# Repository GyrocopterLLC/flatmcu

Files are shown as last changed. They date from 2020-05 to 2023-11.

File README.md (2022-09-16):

# flatmcu
Hardware design for the flatmcu - an STM32G4 based BLDC / FOC motor controller.

## Features
All schematic and layout was created with KiCad EDA (https://kicad.org).

The controller is based on the STM32G473CB microcontroller from ST Microelectronics. It contains an ARM Cortex-M4 core at up to 170MHz. The three-phase bridge driver is the TI DRV8353RS, which also contains shunt resistor current sensors and a 95V buck regulator.

The MOSFETs in the three-phase bridge (Toshiba TPW4R50ANH) are dual-side cooling. There's a large metal pad on top of them. A heatsink should be attached there. The opposite side of the board is intended for soldering on the large battery and phase wires.

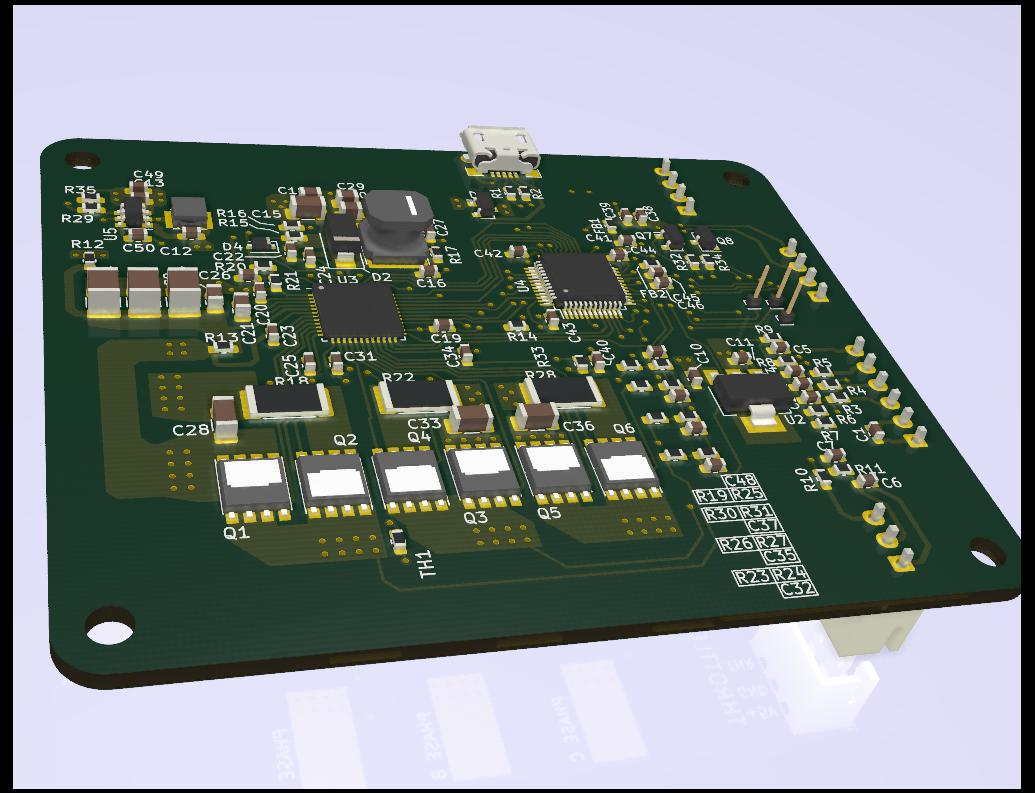
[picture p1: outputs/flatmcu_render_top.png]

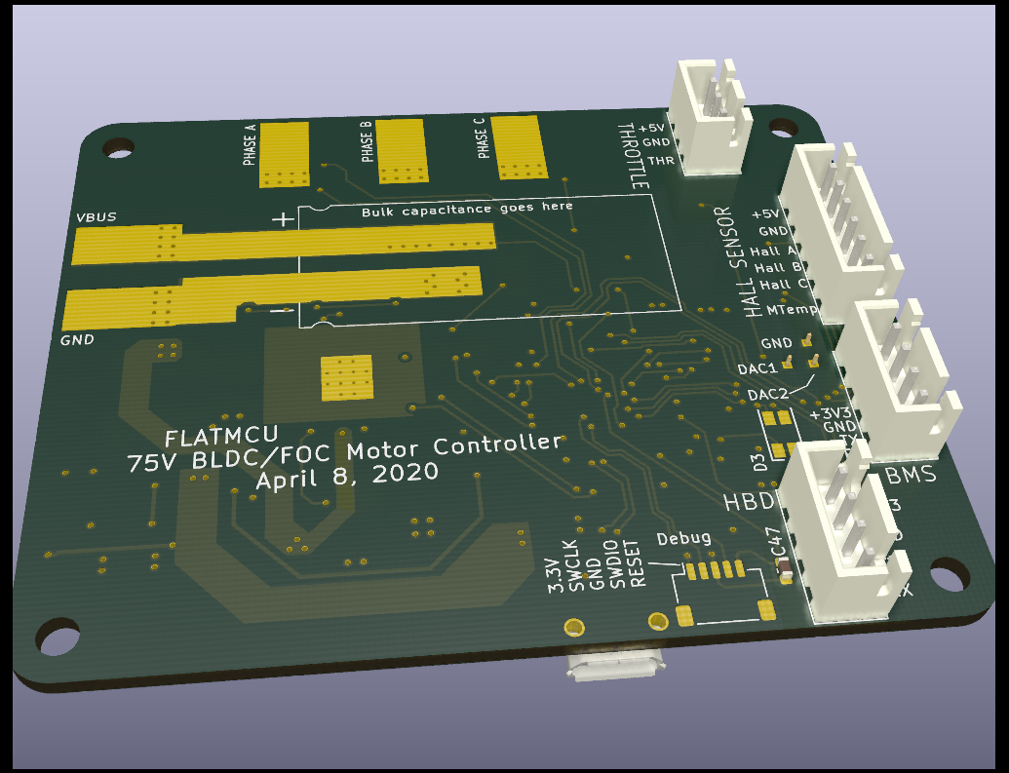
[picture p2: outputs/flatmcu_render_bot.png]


## Schematic
### Main
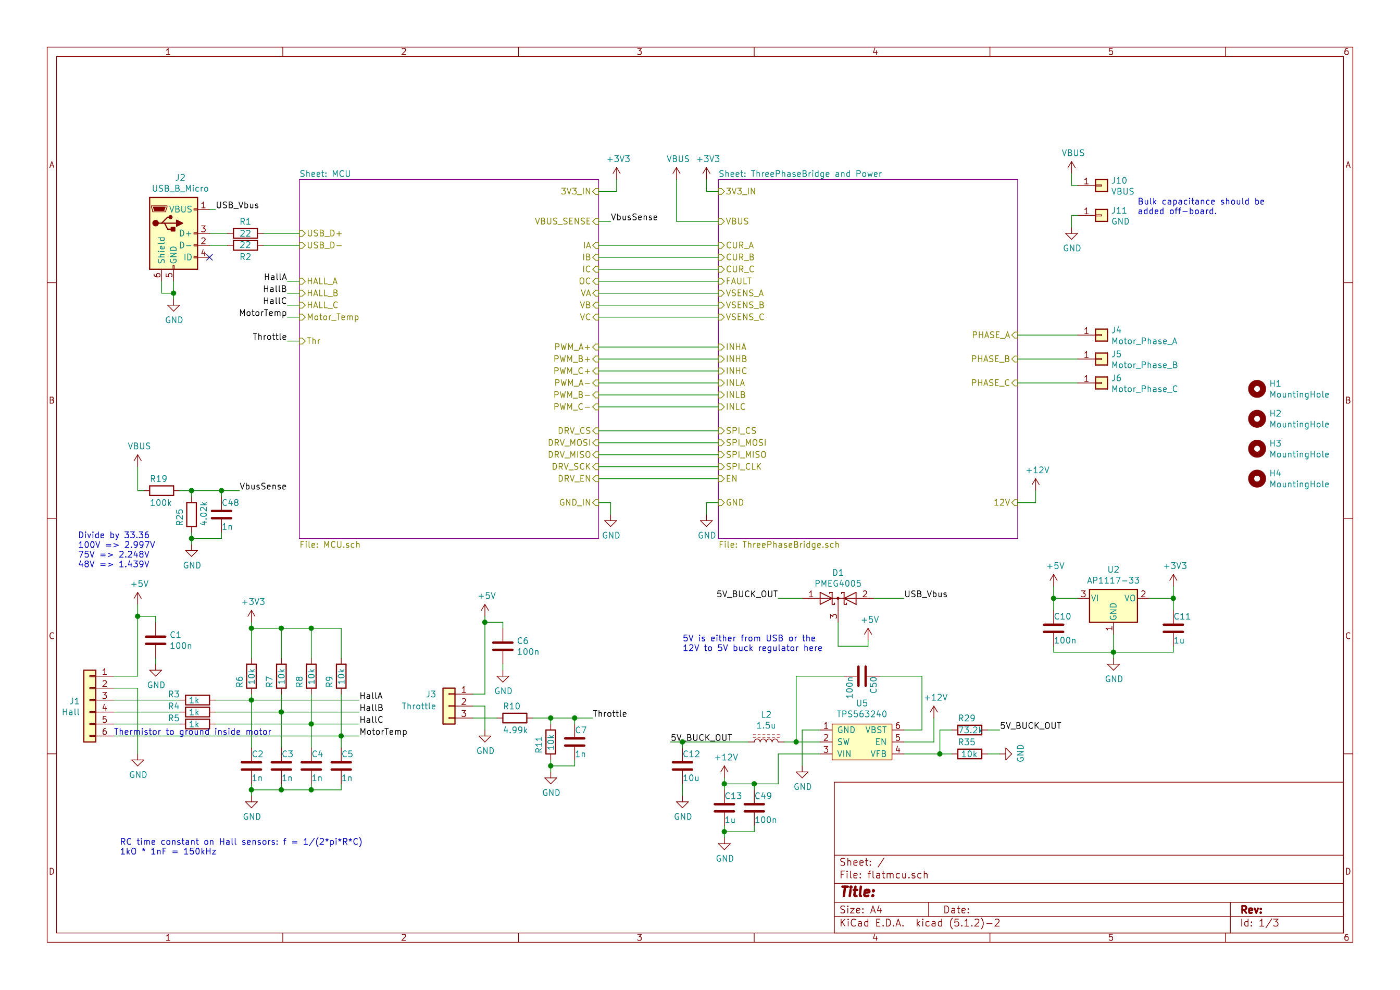
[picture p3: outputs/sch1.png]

### Microcontroller
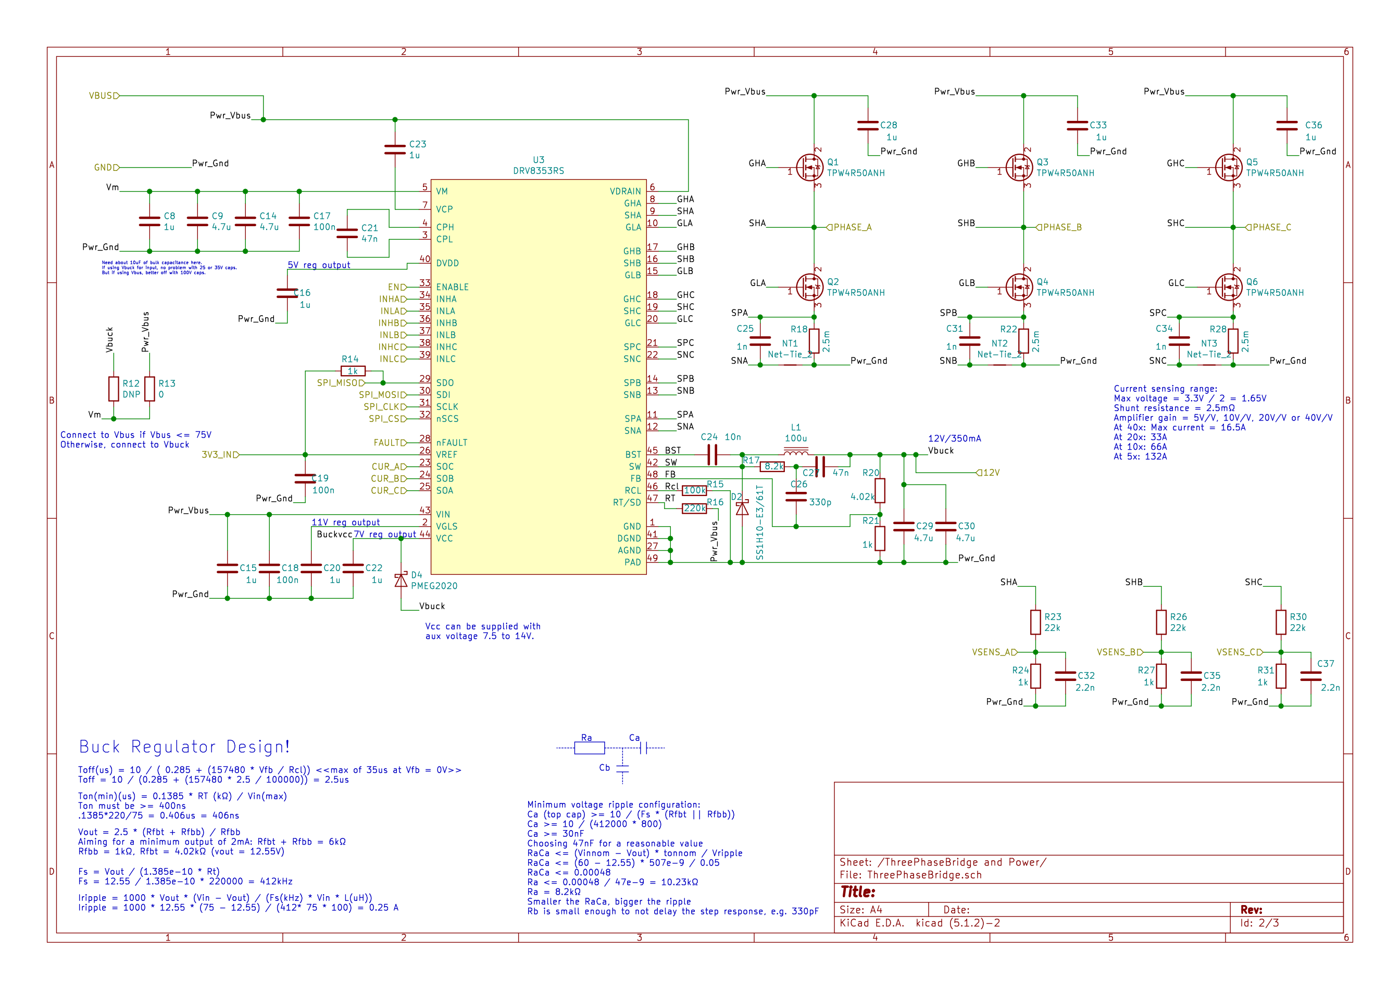
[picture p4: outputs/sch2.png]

### Three-phase bridge
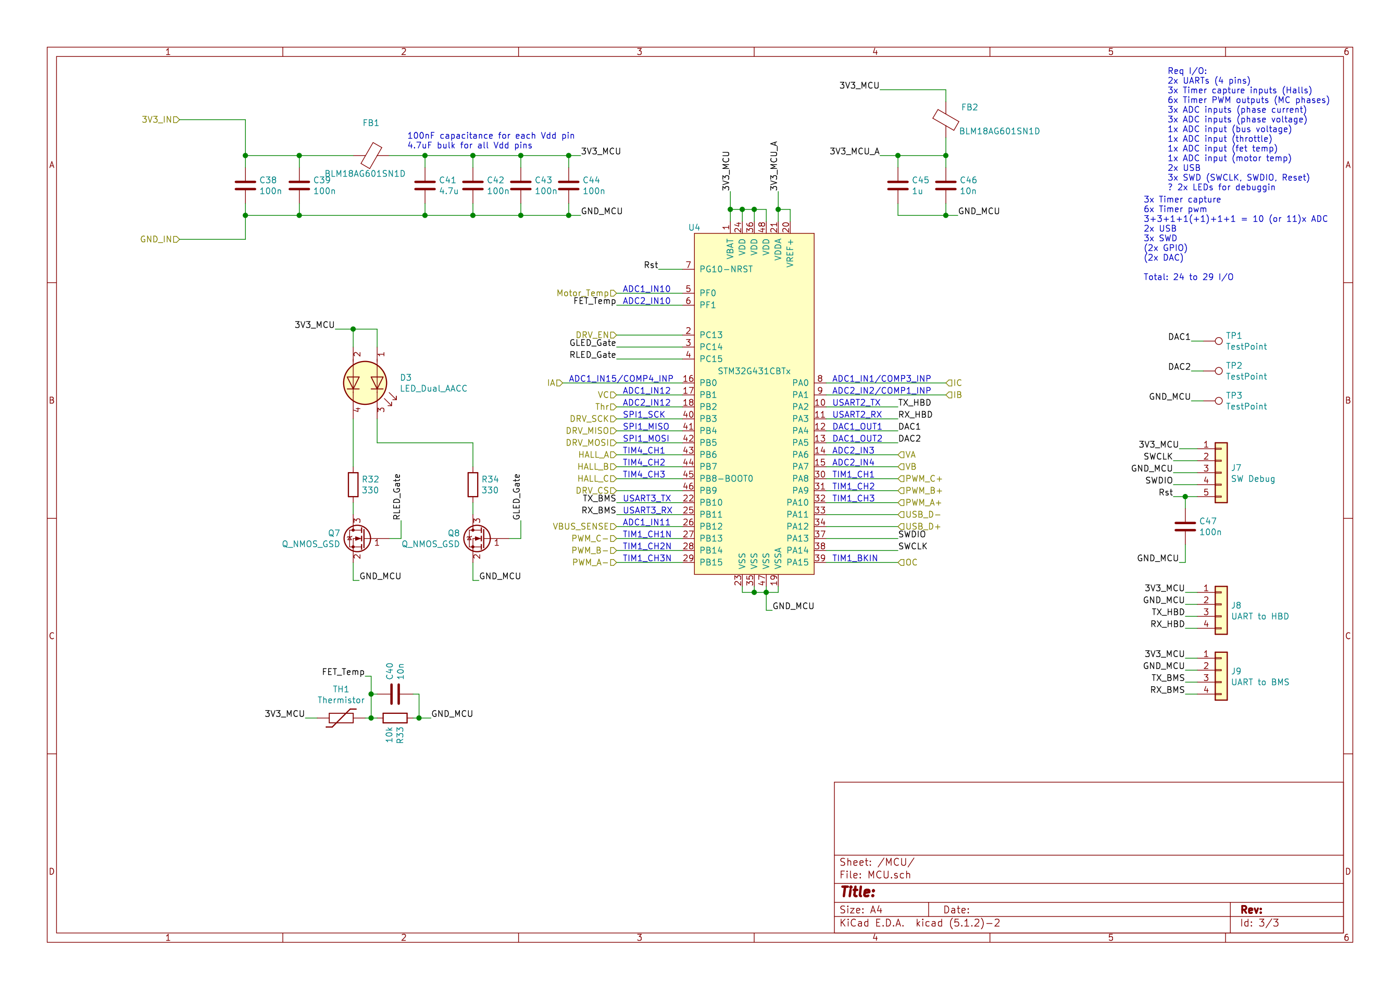
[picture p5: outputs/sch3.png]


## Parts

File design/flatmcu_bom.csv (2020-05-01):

*** Bill of Materials ***
* Note: Many of the resistors and capacitors do not have specific part numbers listed. Substitute with any that meet the value / footprint / voltage specs. *
* Suggest to use X5R/X7R capacitors or better. *
Part No | Value | Footprint | Qty | Refs
??? | 100n/100V | C0805 | 2 | C17, C18
CL10A104KA8NNNC | 100n/25V | C0603 | 11 | C1,C10,C19,C38, C42, C43, C44, C47, C49, C50, C6
??? | 1u/16V | C0603 | 8 | C11, C13, C16, C20, C22, C23, C39, C45
??? | 10n/50V | C0603 | 3 | C24, C40, C46
CRM188R61A106KE69D | 10u/10V | C0603 | 1 | C12
??? | 1n/50V | C0603 | 9 | C2, C3, C4, C5, C7, C25, C31, C34, C48
GCM21BC72A105KE36L | 1u/100V | C0805 | 5 | C8, C15, C28, C33, C36
??? | 2.2n/50V | C0603 | 3 | C32, C35, C37
??? | 330p/50V | C0603 | 1 | C26
??? | 4.7u/6.3V | C0603 | 1 | C41
??? | 4.7u/16V | C0805 | 2 | C29, C30
GCM32DC72A475KE02L | 4.7u/100V | C1210 | 2 | C9, C14
??? | 47n/16V | C0603 | 1 | C27
CL21B473KCCWPNC | 47n/100V | C0805 | 1 | C21
PMEG4005CT,215 | Dual Schottky 40V 500mA | SOT23 | 1 | D1
SS1H10-E3/61T | Schottky 100V 1A | SMA | 1 | D2
LTST-C155GEKT | Red/Green LED | 4-SMD | 1 | D3
PMEG2020EJ,115 | Schottky 20V 2A | SOD323F | 1 | D4
TPW4R50ANH | N-CH 100V 92A | 8DSOP | 6 | Q1, Q2, Q3, Q4, Q5, Q6
AO3400A | N-CH 30V 6.7A | SOT23 | 2 | Q7, Q8
NR6045T101M | 100uH 800mA | 6x6mm | 1 | L1
SRN3015-1R5Y | 1.5uH 2.1A | 3x3mm | 1 | L2
BLM18AG601SN1D | Ferrite Bead 600ohm | R0603 | 2 | FB1, FB2
??? | 0R | R0603 | 1 | R13
??? | 33R | R0603 | 2 | R1, R2
??? | 330R | R0603 | 2 | R32, R34
??? | 100k | R0603 | 2 | R15, R19
??? | 10k | R0603 | 7 | R6, R7, R8, R9, R11, R33, R35
??? | 1k | R0603 | 8 | R3, R4, R5, R14, R21, R24, R27, R31
ERJ-M1WTF2M0U | 0R002 | R2512 | 3 | R18, R22, R28
ERJ-3EKF2203V | 220k | R0603 | 1 | R16
??? | 22k | R0603 | 3 | R23, R26, R30
??? | 4.02k | R0603 | 2 | R20, R25
??? | 4.99k | R0603 | 1 | R10
??? | 73.2k | R0603 | 1 | R29
??? | 8.2k | R0603 | 1 | R17
ERT-J1VR103J | NTC Thermistor 10k | R0603 | 1 | TH1
B5B-XH-A(LF)(SN) | 5 pin JST XH | B5B-XH-A(LF)(SN) | 1 | J1
10118193-0001LF | USB Micro B THT | 10118193-0001LF | 1 | J2
B3B-XH-A(LF)(SN) | 3 pin JST XH | B3B-XH-A(LF)(SN) | 1 | J3
BM05B-SRSS-TB(LF)(SN) | 5 pin JST SR | BM05B-SRSS-TB(LF)(SN) | 1 | J7
B4B-XH-A(LF)(SN) | 4 pin JST XH | B4B-XH-A(LF)(SN) | 2 | J8, J9
AP1117E33G-13 | LDO 18Vin 3.3Vout 1.1A | SOT223 | 1 | U2
DRV8353RSRGZT | Three phase driver | 48QFN | 1 | U3
STM32G473CET6 | MCU Arm Cortex-M4 | 48LQFP | 1 | U4
TPS563240DDCT | Buck Reg Adj 3A 17Vin | SOT23-6 | 1 | U5

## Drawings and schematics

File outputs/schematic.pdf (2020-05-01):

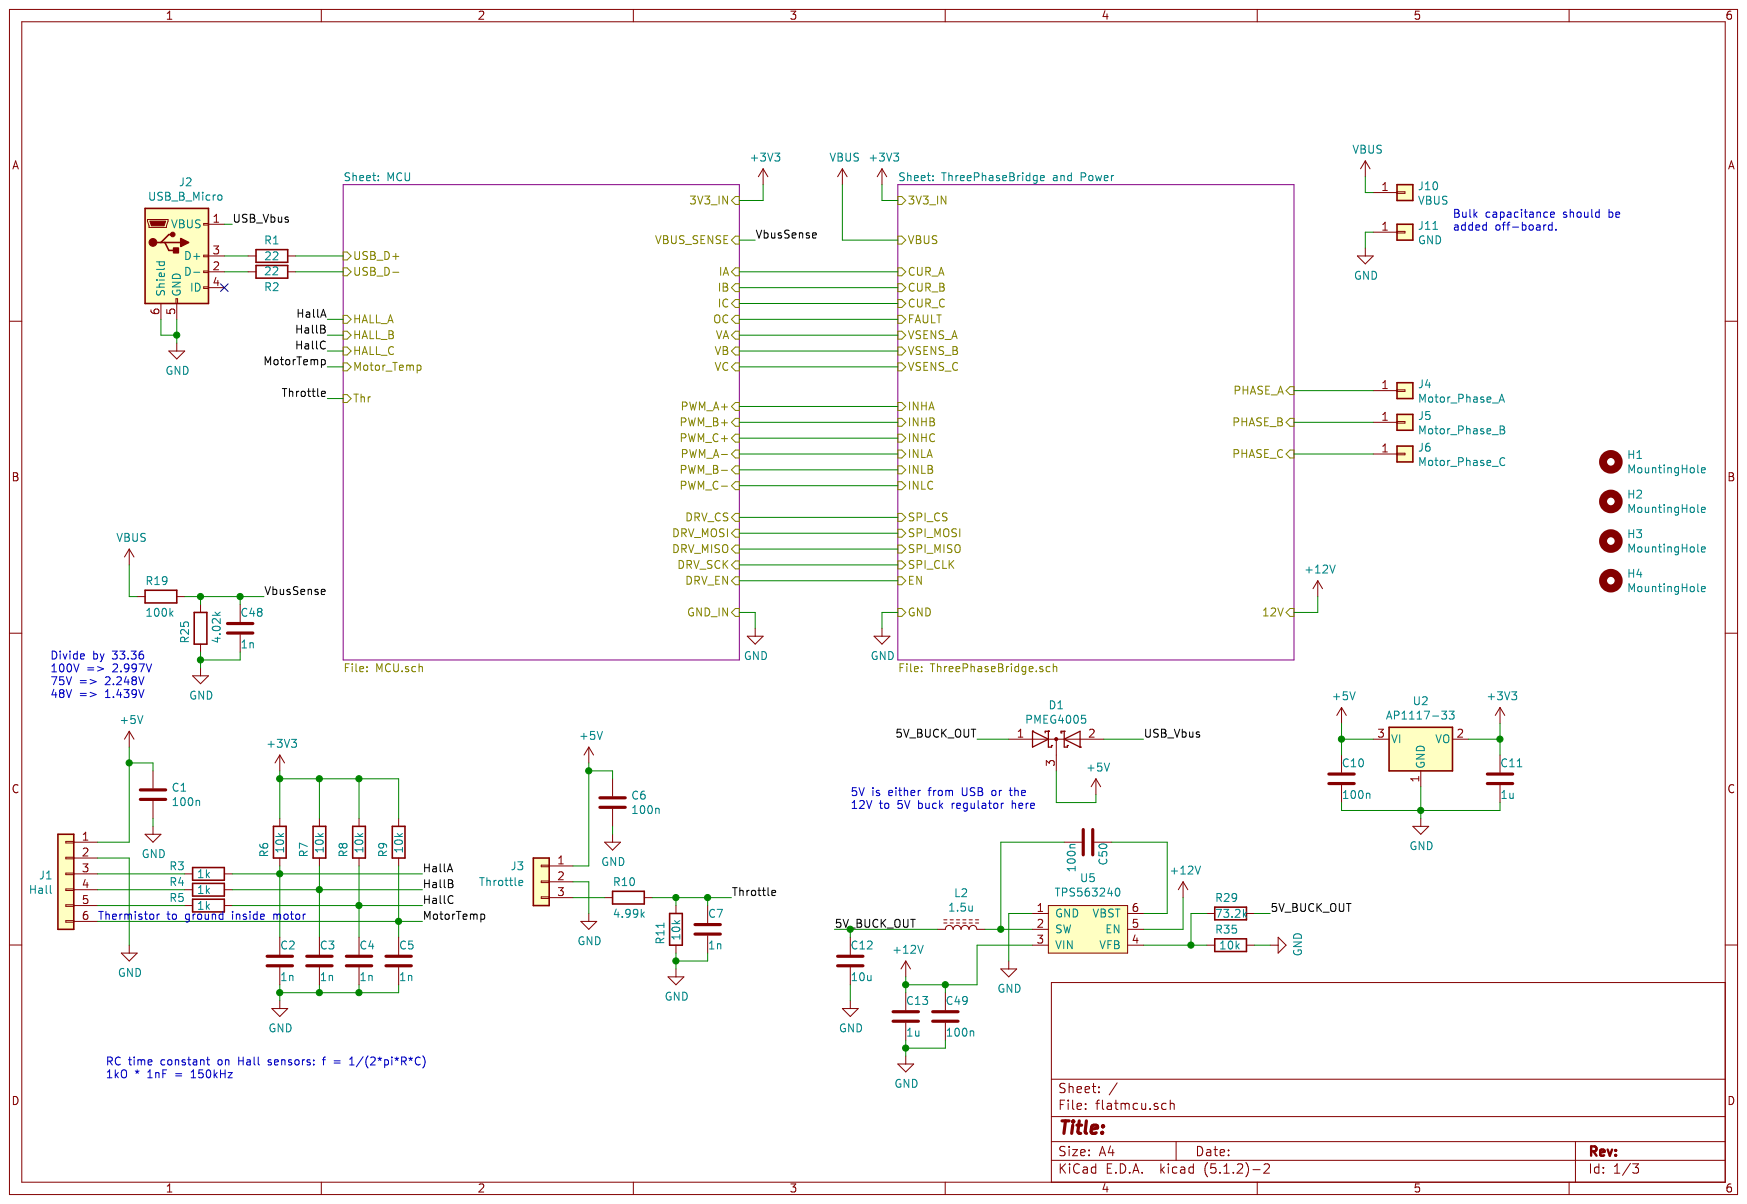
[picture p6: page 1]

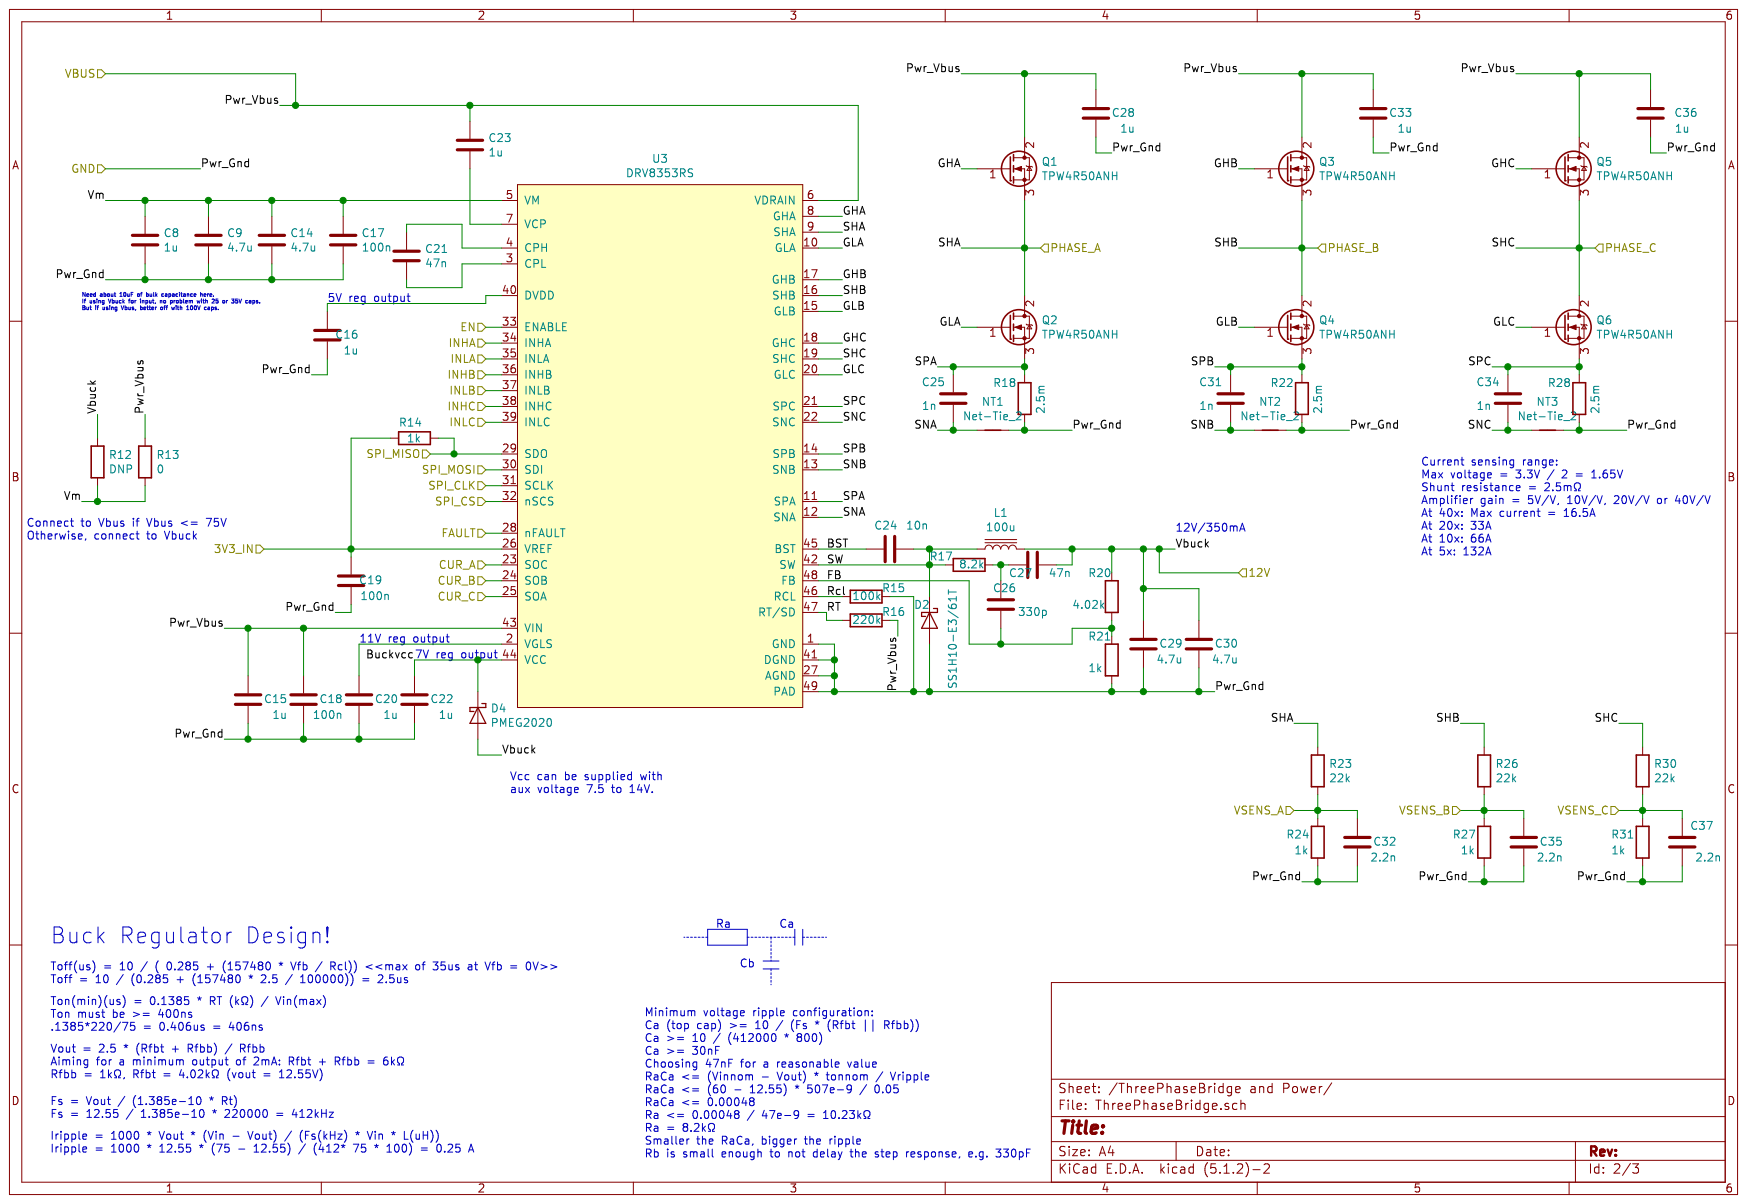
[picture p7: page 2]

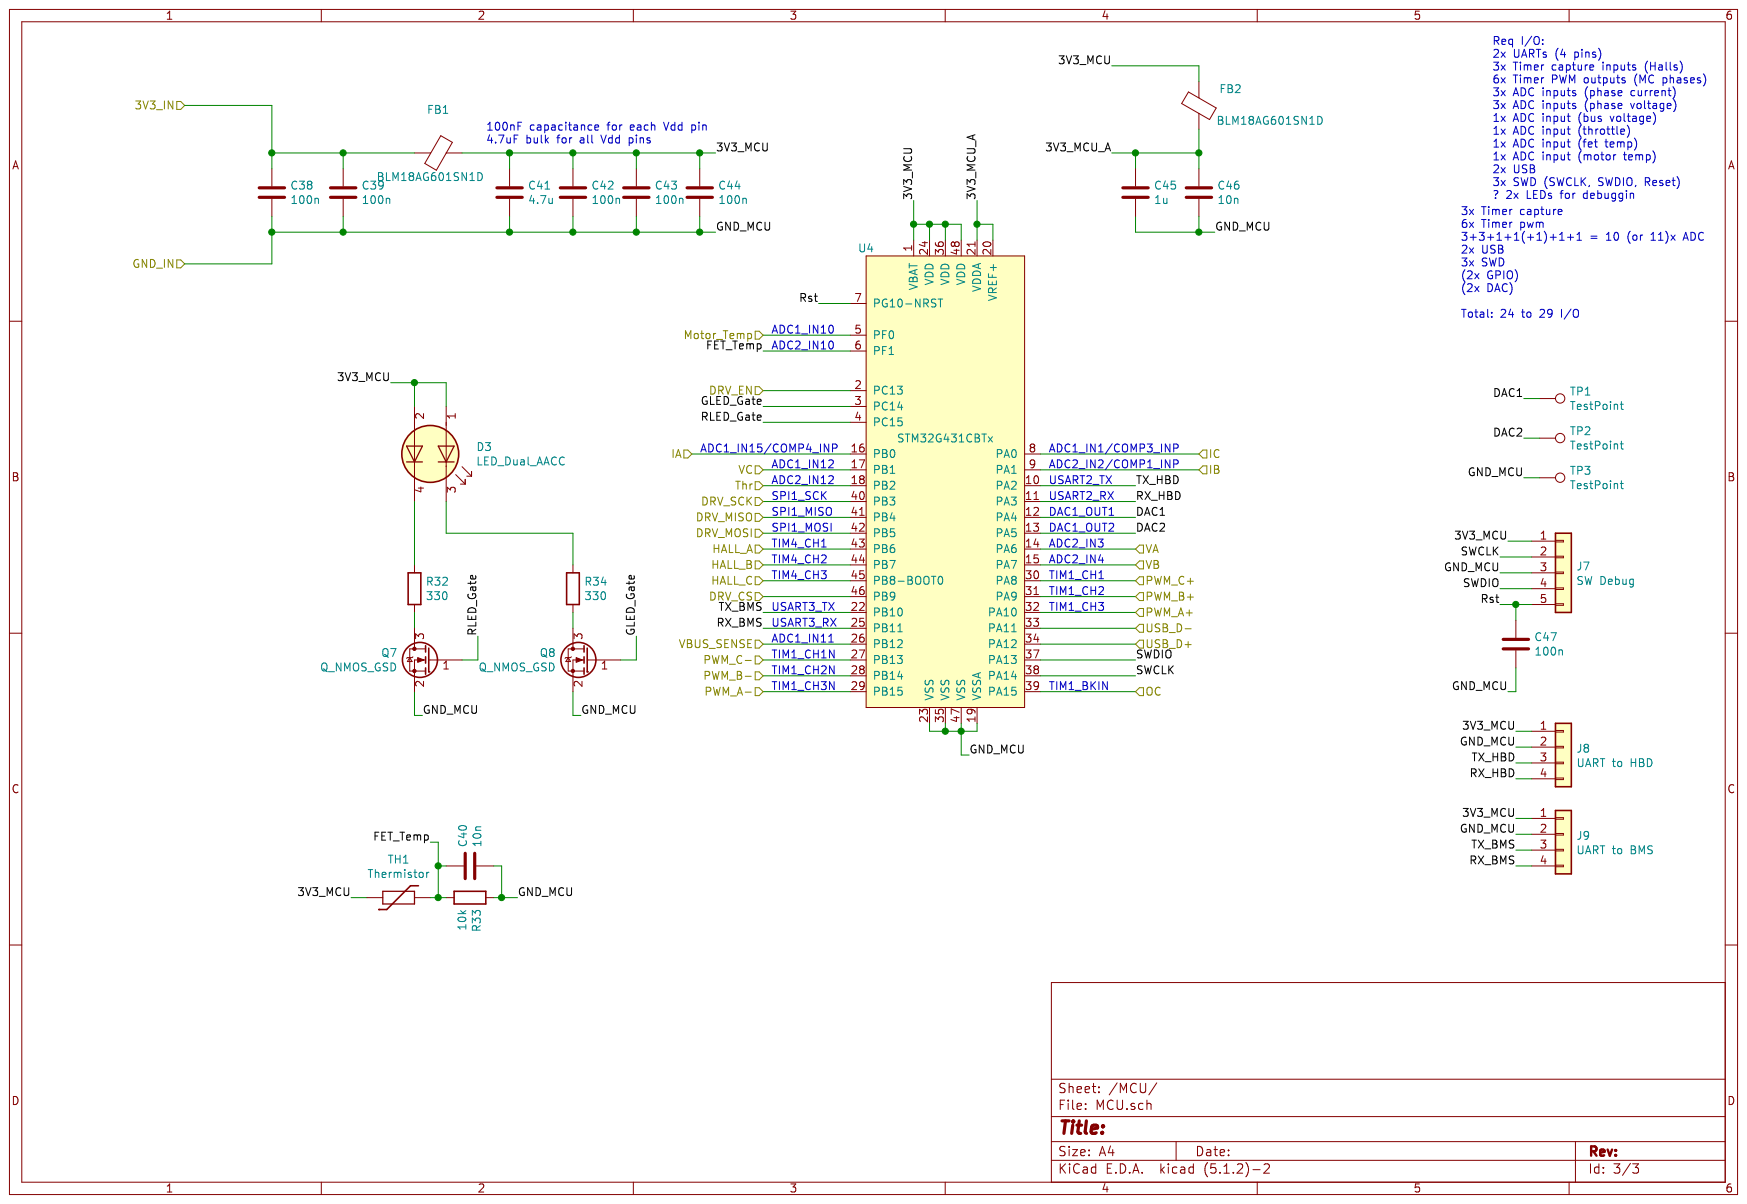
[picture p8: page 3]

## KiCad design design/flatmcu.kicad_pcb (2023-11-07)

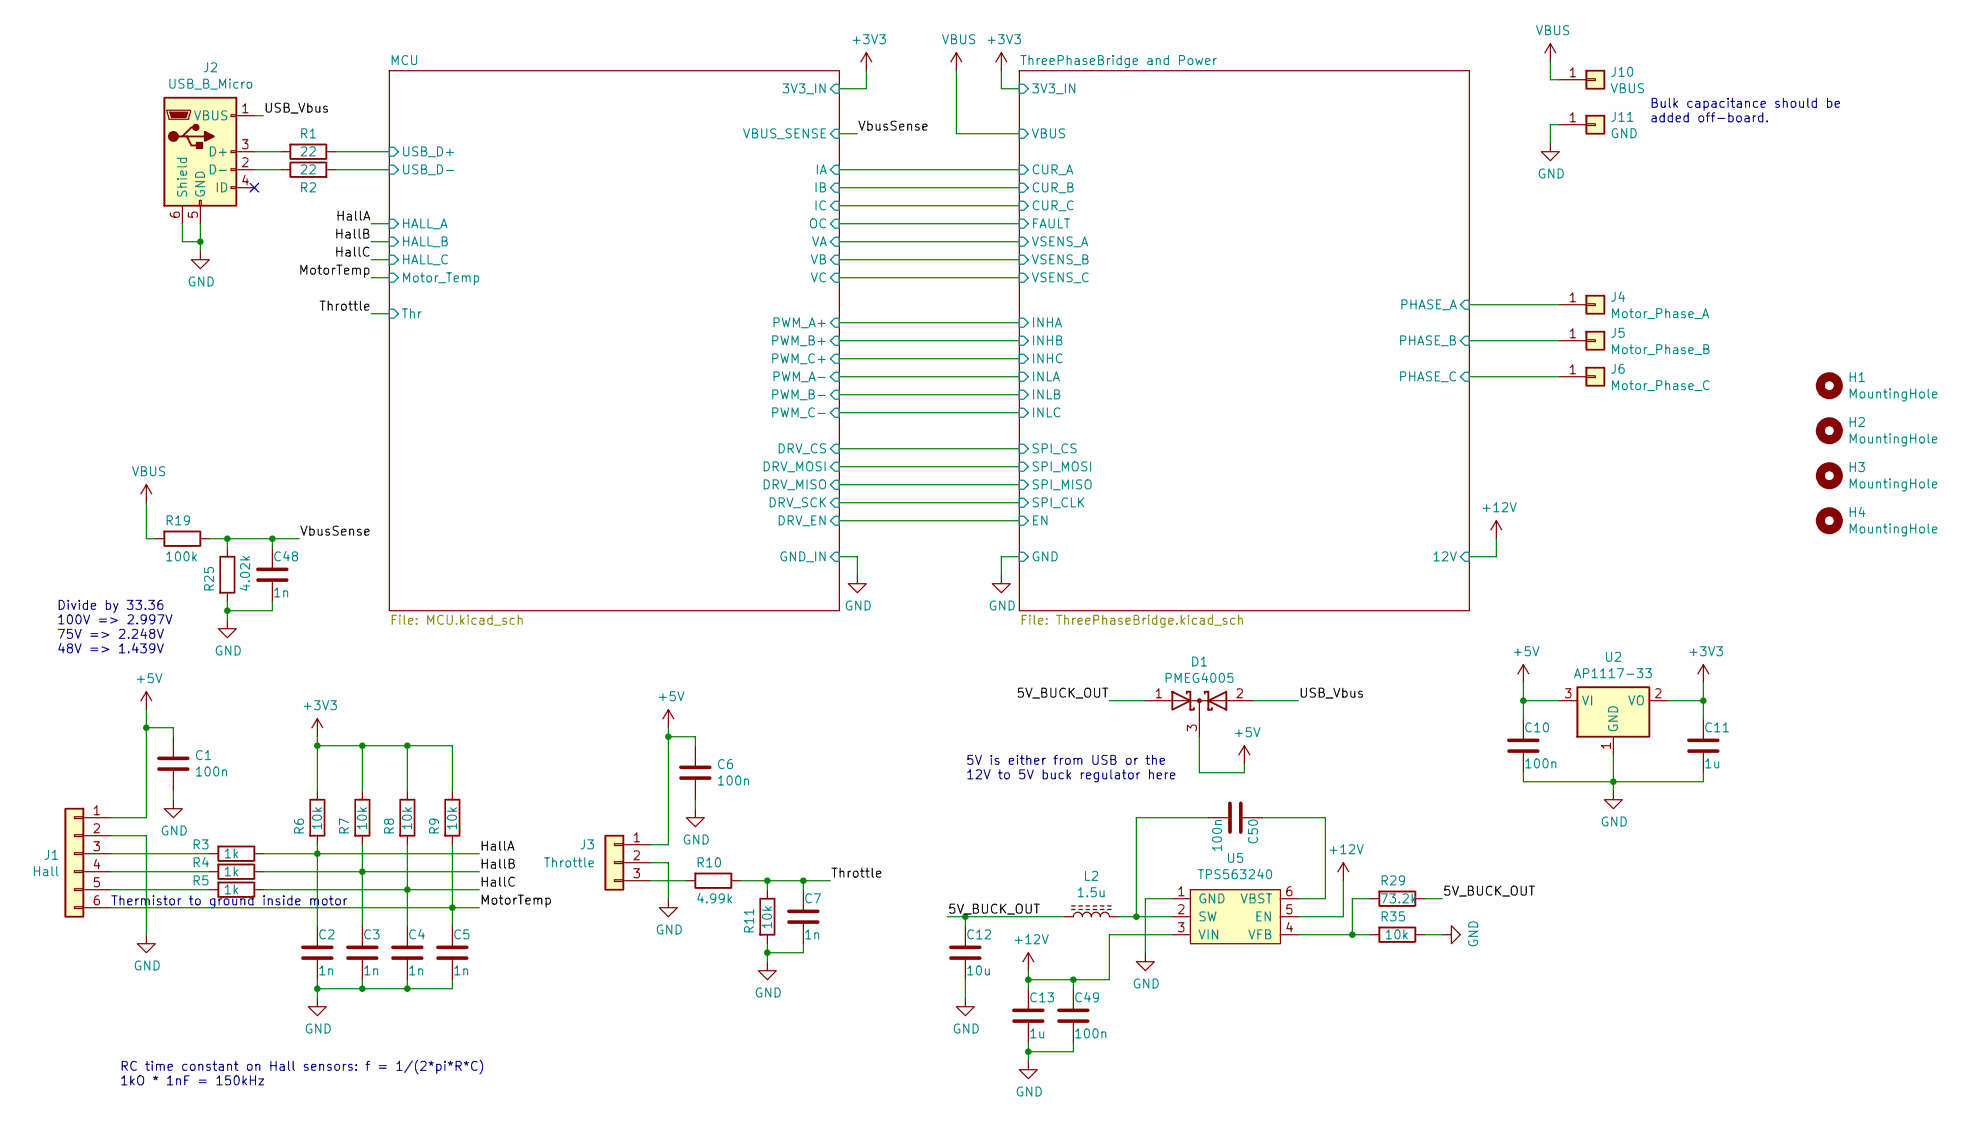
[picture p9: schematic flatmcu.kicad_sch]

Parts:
C1, C6, C10: 100n; C_0603_1608Metric; Voltage 6.3V
C2, C3, C4, C5, C7, C48: 1n; C_0603_1608Metric; Voltage 6.3V
C11: 1u; C_0603_1608Metric; Voltage 6.3V
C12: 10u; C_0603_1608Metric; Voltage 6.3V
C13: 1u; C_0603_1608Metric; Voltage 16V
C49, C50: 100n; C_0603_1608Metric; Voltage 16V
D1: PMEG4005; SOT-23
H1, H2, H3, H4: MountingHole; MountingHole_3.2mm_M3
J1: Hall; JST_XH_B6B-XH-A_1x06_P2.50mm_Vertical
J2: USB_B_Micro; USB_Micro_B_Female_10118193-0001LF
J3: Throttle; JST_XH_B3B-XH-A_1x03_P2.50mm_Vertical
J4: Motor_Phase_A; SolderWirePad_1x01_SMD_5x10mm
J5: Motor_Phase_B; SolderWirePad_1x01_SMD_5x10mm
J6: Motor_Phase_C; SolderWirePad_1x01_SMD_5x10mm
J10: VBUS; SolderWirePad_1x01_SMD_5x10mm
J11: GND; SolderWirePad_1x01_SMD_5x10mm
L2: 1.5u; Bourns_SRN3015
R1, R2: 22; R_0603_1608Metric
R3, R4, R5: 1k; R_0603_1608Metric
R6, R7, R8, R9, R11, R35: 10k; R_0603_1608Metric
R10: 4.99k; R_0603_1608Metric
R19: 100k; R_0603_1608Metric
R25: 4.02k; R_0603_1608Metric
R29: 73.2k; R_0603_1608Metric
U2: AP1117-33; SOT-223-3_TabPin2
U5: TPS563240; SOT-23-6

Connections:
+3V3: C11.1, R6.1, R7.1, R8.1, R9.1, U2.2 (VO); also elsewhere on the board
+5V: C1.1, C6.1, C10.1, D1.3 (K), J1.1, J3.1, U2.3 (VI)
+12V: C13.1, C49.1, U5.3 (VIN), U5.5 (EN); also elsewhere on the board
/5V_BUCK_OUT: C12.1, D1.1 (A), L2.1, R29.1
/HallA: C2.1, R3.1, R6.2; also elsewhere on the board
/HallB: C3.1, R4.1, R7.2; also elsewhere on the board
/HallC: C4.1, R5.1, R8.2; also elsewhere on the board
/MCU/USB_D+: R1.1; also elsewhere on the board
/MCU/USB_D-: R2.2; also elsewhere on the board
/MotorTemp: C5.1, J1.6, R9.2; also elsewhere on the board
/ThreePhaseBridge and Power/PHASE_A: J4.1; also elsewhere on the board
/ThreePhaseBridge and Power/PHASE_B: J5.1; also elsewhere on the board
/ThreePhaseBridge and Power/PHASE_C: J6.1; also elsewhere on the board
/Throttle: C7.1, R10.1, R11.1; also elsewhere on the board
/USB_Vbus: D1.2 (A), J2.1 (VBUS)
/VbusSense: C48.1, R19.1, R25.1; also elsewhere on the board
GND: C1.2, C2.2, C3.2, C4.2, C5.2, C6.2, C7.2, C10.2, C11.2, C12.2, C13.2, C48.2, C49.2, J1.2, J2.5 (GND), J2.6 (Shield), J3.2, J11.1, R11.2, R25.2, R35.1, U2.1 (GND), U5.1 (GND); also elsewhere on the board
unnamed: C50.1, U5.6 (VBST)
unnamed: C50.2, L2.2, U5.2 (SW)
unnamed: J1.3, R3.2
unnamed: J1.4, R4.2
unnamed: J1.5, R5.2
unnamed: J2.2 (D-), R2.1
unnamed: J2.3 (D+), R1.2
unnamed: J3.3, R10.2
unnamed: R29.2, R35.2, U5.4 (VFB)
VBUS: J10.1, R19.2; also elsewhere on the board

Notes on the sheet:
RC time constant on Hall sensors: f = 1/(2*pi*R*C) 1kO * 1nF = 150kHz
Divide by 33.36 100V => 2.997V 75V => 2.248V 48V => 1.439V
Thermistor to ground inside motor
Bulk capacitance should be added off-board.
5V is either from USB or the 12V to 5V buck regulator here

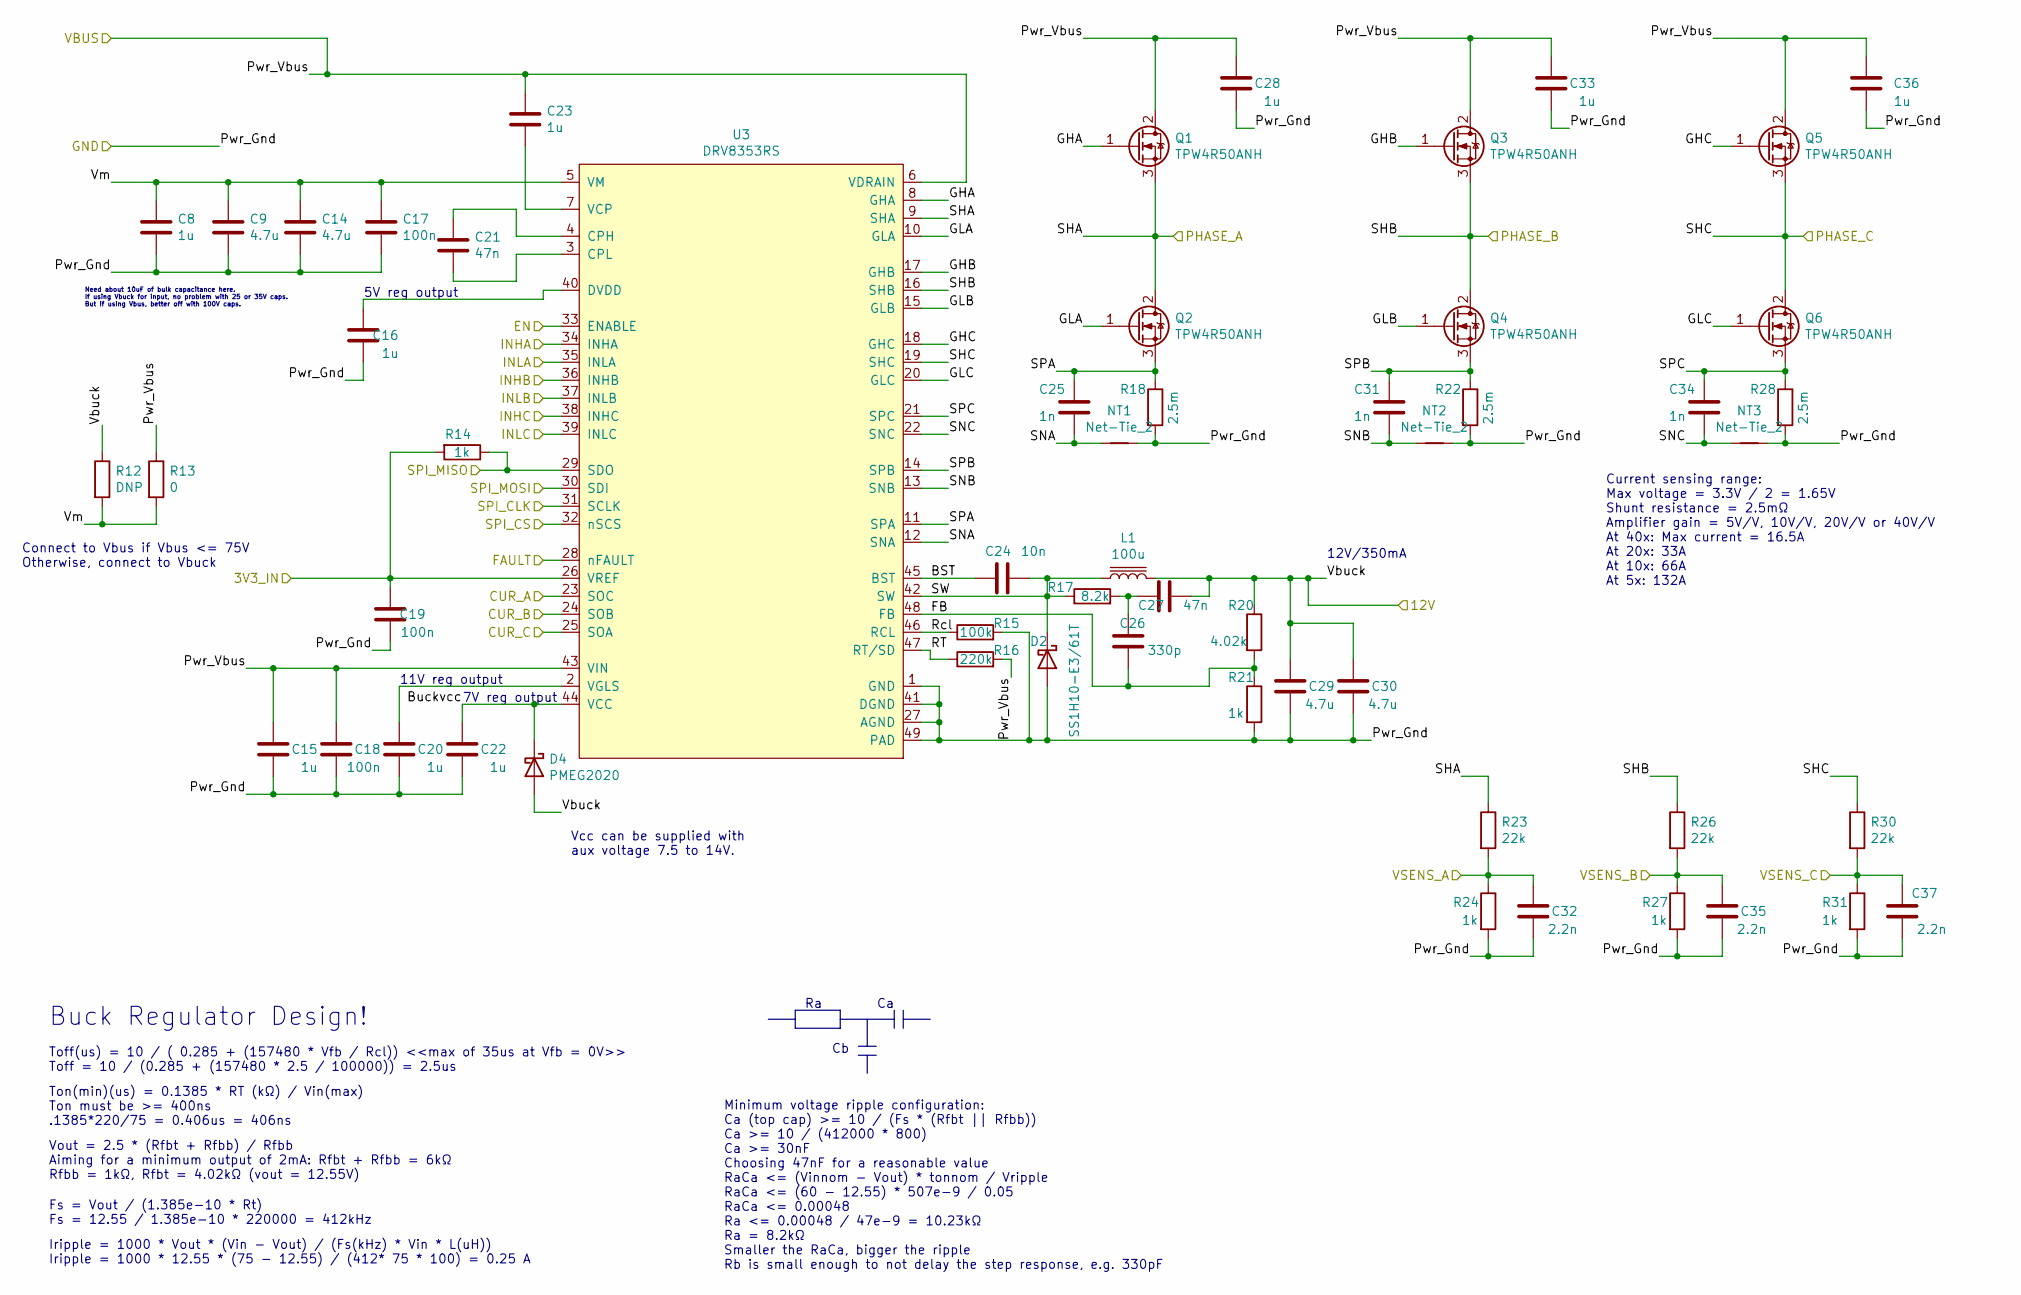
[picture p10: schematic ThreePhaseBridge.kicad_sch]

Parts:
C8: 1u; C_1210_3225Metric; Voltage 100V
C9, C14: 4.7u; C_1210_3225Metric; Voltage 100V
C15, C28, C33, C36: 1u; C_1206_3216Metric; Voltage 100V
C16: 1u; C_0603_1608Metric; Voltage 6.3V
C17, C18: 100n; C_0805_2012Metric; Voltage 100V
C19: 100n; C_0603_1608Metric; Voltage 6.3V
C20, C22, C23: 1u; C_0603_1608Metric; Voltage 16V
C21: 47n; C_0805_2012Metric; Voltage 100V
C24: 10n; C_0603_1608Metric; Voltage 16V
C25, C31, C34: 1n; C_0603_1608Metric
C26: 330p; C_0603_1608Metric; Voltage 16V
C27: 47n; C_0603_1608Metric; Voltage 16V
C29, C30: 4.7u; C_0805_2012Metric; Voltage 16V
C32, C35, C37: 2.2n; C_0603_1608Metric; Voltage 16V
D2: SS1H10-E3/61T; D_SMA
D4: PMEG2020; D_SOD-323F
L1: 100u; NR6045
NT1, NT2, NT3: Net-Tie_2; NetTie-2_SMD_Pad0.5mm
Q1, Q2, Q3, Q4, Q5, Q6: TPW4R50ANH; Toshiba_DSOP-Advance
R12: DNP; R_0603_1608Metric
R13: 0; R_0603_1608Metric
R14, R21, R24, R27, R31: 1k; R_0603_1608Metric
R15: 100k; R_0603_1608Metric
R16: 220k; R_0603_1608Metric
R17: 8.2k; R_0603_1608Metric
R18, R22, R28: 2.5m; R_2512_6332Metric
R20: 4.02k; R_0603_1608Metric
R23, R26, R30: 22k; R_0603_1608Metric
U3: DRV8353RS; TI-RGZ-48-QFN

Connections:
+3V3: C19.2, R14.2, U3.26 (VREF); also elsewhere on the board
+12V: C27.1, C29.2, C30.2, D4.2 (A), L1.2, R12.1, R20.1; also elsewhere on the board
/MCU/DRV_CS: U3.32 (nSCS); also elsewhere on the board
/MCU/DRV_EN: U3.33 (ENABLE); also elsewhere on the board
/MCU/DRV_MISO: R14.1, U3.29 (SDO); also elsewhere on the board
/MCU/DRV_MOSI: U3.30 (SDI); also elsewhere on the board
/MCU/DRV_SCK: U3.31 (SCLK); also elsewhere on the board
/MCU/VA: C32.2, R23.2, R24.1; also elsewhere on the board
/MCU/VB: C35.2, R26.2, R27.1; also elsewhere on the board
/MCU/VC: C37.2, R30.2, R31.1; also elsewhere on the board
/ThreePhaseBridge and Power/BST: C24.2, U3.45 (BST)
/ThreePhaseBridge and Power/Buckvcc: C22.2, D4.1 (K), U3.44 (VCC)
/ThreePhaseBridge and Power/CUR_A: U3.23 (SOC); also elsewhere on the board
/ThreePhaseBridge and Power/CUR_B: U3.24 (SOB); also elsewhere on the board
/ThreePhaseBridge and Power/CUR_C: U3.25 (SOA); also elsewhere on the board
/ThreePhaseBridge and Power/FAULT: U3.28 (nFAULT); also elsewhere on the board
/ThreePhaseBridge and Power/FB: C26.1, R20.2, R21.1, U3.48 (FB)
/ThreePhaseBridge and Power/GHA: Q1.1 (G), U3.8 (GHA)
/ThreePhaseBridge and Power/GHB: Q3.1 (G), U3.17 (GHB)
/ThreePhaseBridge and Power/GHC: Q5.1 (G), U3.18 (GHC)
/ThreePhaseBridge and Power/GLA: Q2.1 (G), U3.10 (GLA)
/ThreePhaseBridge and Power/GLB: Q4.1 (G), U3.15 (GLB)
/ThreePhaseBridge and Power/GLC: Q6.1 (G), U3.20 (GLC)
/ThreePhaseBridge and Power/INHA: U3.34 (INHA); also elsewhere on the board
/ThreePhaseBridge and Power/INHB: U3.36 (INHB); also elsewhere on the board
/ThreePhaseBridge and Power/INHC: U3.38 (INHC); also elsewhere on the board
/ThreePhaseBridge and Power/INLA: U3.35 (INLA); also elsewhere on the board
/ThreePhaseBridge and Power/INLB: U3.37 (INLB); also elsewhere on the board
/ThreePhaseBridge and Power/INLC: U3.39 (INLC); also elsewhere on the board
/ThreePhaseBridge and Power/PHASE_A: Q1.3 (S), Q2.2 (D), R23.1, U3.9 (SHA); also elsewhere on the board
/ThreePhaseBridge and Power/PHASE_B: Q3.3 (S), Q4.2 (D), R26.1, U3.16 (SHB); also elsewhere on the board
/ThreePhaseBridge and Power/PHASE_C: Q5.3 (S), Q6.2 (D), R30.1, U3.19 (SHC); also elsewhere on the board
/ThreePhaseBridge and Power/RT: R16.1, U3.47 (RT/SD)
/ThreePhaseBridge and Power/Rcl: R15.1, U3.46 (RCL)
/ThreePhaseBridge and Power/SNA: C25.1, NT1.1, U3.12 (SNA)
/ThreePhaseBridge and Power/SNB: C31.1, NT2.1, U3.13 (SNB)
/ThreePhaseBridge and Power/SNC: C34.1, NT3.1, U3.22 (SNC)
/ThreePhaseBridge and Power/SPA: C25.2, Q2.3 (S), R18.1, U3.11 (SPA)
/ThreePhaseBridge and Power/SPB: C31.2, Q4.3 (S), R22.1, U3.14 (SPB)
/ThreePhaseBridge and Power/SPC: C34.2, Q6.3 (S), R28.1, U3.21 (SPC)
/ThreePhaseBridge and Power/SW: C24.1, D2.1 (K), L1.1, R17.1, U3.42 (SW)
/ThreePhaseBridge and Power/Vm: C8.1, C9.1, C14.1, C17.1, R12.2, R13.2, U3.5 (VM)
GND: C8.2, C9.2, C14.2, C15.1, C16.1, C17.2, C18.1, C19.1, C20.1, C22.1, C28.1, C29.1, C30.1, C32.1, C33.1, C35.1, C36.1, C37.1, D2.2 (A), NT1.2, NT2.2, NT3.2, R15.2, R18.2, R21.2, R22.2, R24.2, R27.2, R28.2, R31.2, U3.1 (GND), U3.27 (AGND), U3.41 (DGND), U3.49 (PAD); also elsewhere on the board
unnamed: C16.2, U3.40 (DVDD)
unnamed: C20.2, U3.2 (VGLS)
unnamed: C21.1, U3.4 (CPH)
unnamed: C21.2, U3.3 (CPL)
unnamed: C23.2, U3.7 (VCP)
unnamed: C26.2, C27.2, R17.2
VBUS: C15.2, C18.2, C23.1, C28.2, C33.2, C36.2, Q1.2 (D), Q3.2 (D), Q5.2 (D), R13.1, R16.2, U3.6 (VDRAIN), U3.43 (VIN); also elsewhere on the board

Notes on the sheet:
Buck Regulator Design!
Current sensing range: Max voltage = 3.3V / 2 = 1.65V Shunt resistance = 2.5mΩ Amplifier gain = 5V/V, 10V/V, 20V/V or 40V/V At 40x: Max current = 16.5A At 20x: 33A At 10x: 66A At 5x: 132A
Vout = 2.5 * (Rfbt + Rfbb) / Rfbb Aiming for a minimum output of 2mA: Rfbt + Rfbb = 6kΩ Rfbb = 1kΩ, Rfbt = 4.02kΩ (vout = 12.55V)
5V reg output
Vcc can be supplied with aux voltage 7.5 to 14V.
Minimum voltage ripple configuration: Ca (top cap) >= 10 / (Fs * (Rfbt || Rfbb)) Ca >= 10 / (412000 * 800) Ca >= 30nF Choosing 47nF for a reasonable value RaCa <= (Vinnom - Vout) * tonnom / Vripple RaCa <= (60 - 12.55) * 507e-9 / 0.05 RaCa <= 0.00048 Ra <= 0.00048 / 47e-9 = 10.23kΩ Ra = 8.2kΩ Small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
12V/350mA
11V reg output
Iripple = 1000 * Vout * (Vin - Vout) / (Fs(kHz) * Vin * L(uH)) Iripple = 1000 * 12.55 * (75 - 12.55) / (412* 75 * 100) = 0.25 A
Ton(min)(us) = 0.1385‬ * RT (kΩ) / Vin(max) Ton must be >= 400ns .1385*220/75 = 0.406us = 406ns
7V reg output
Connect to Vbus if Vbus <= 75V Otherwise, connect to Vbuck
Fs = Vout / (1.385e-10 * Rt) Fs = 12.55 / 1.385e-10 * 220000 = 412kHz
Toff(us) = 10 / ( 0.285 + (157480 * Vfb / Rcl)) <<max of 35us at Vfb = 0V>> Toff = 10 / (0.285 + (157480 * 2.5 / 100000)) = 2.5us
Need about 10uF of bulk capacitance here. If using Vbuck for input, no problem with 25 or 35V caps. But if using Vbus, better off with 100V caps.

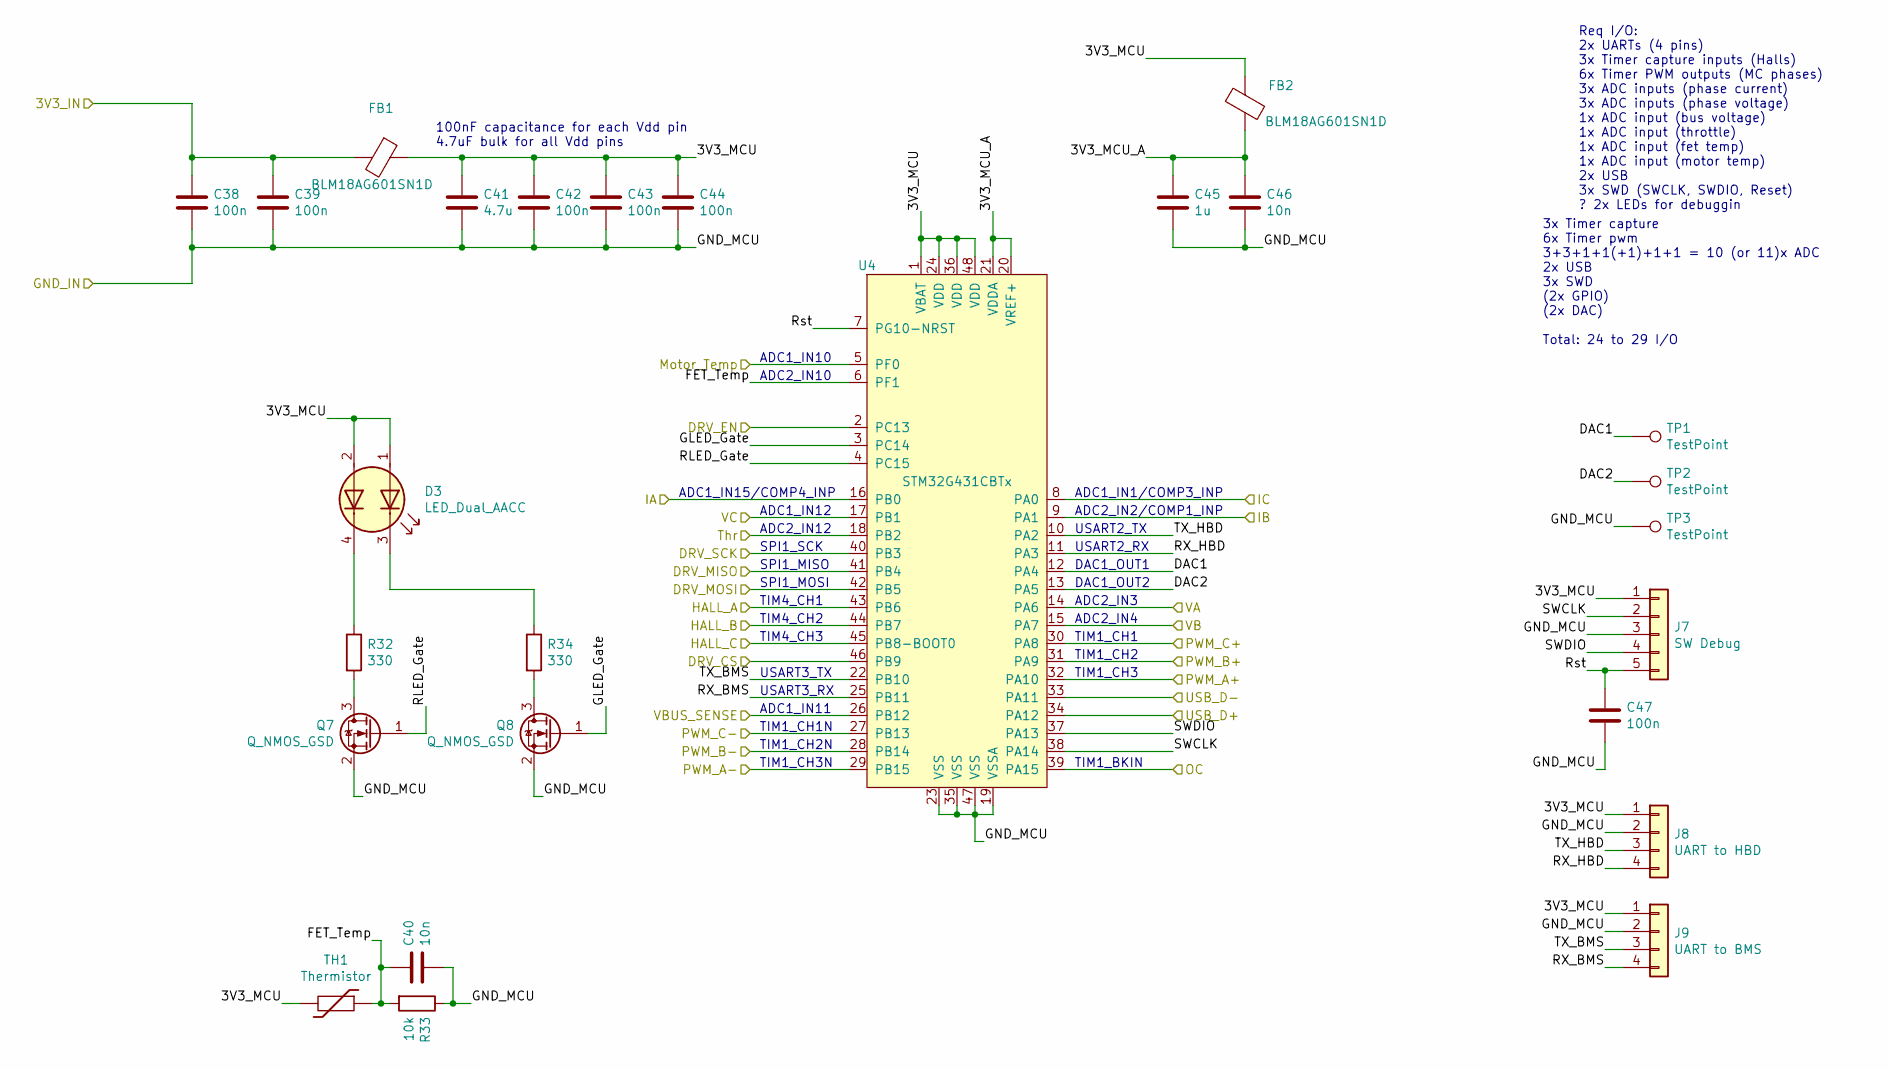
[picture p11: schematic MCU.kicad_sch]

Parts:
C38, C39, C42, C43, C44, C47: 100n; C_0603_1608Metric
C40, C46: 10n; C_0603_1608Metric
C41: 4.7u; C_0603_1608Metric
C45: 1u; C_0603_1608Metric
D3: LED_Dual_AACC; LED_RGB_1210
FB1, FB2: BLM18AG601SN1D; R_0603_1608Metric
J7: SW Debug; JST_SH_SM05B-SRSS-TB_1x05-1MP_P1.00mm_Horizontal
J8: UART to HBD; JST_XH_B4B-XH-A_1x04_P2.50mm_Vertical
J9: UART to BMS; JST_XH_B4B-XH-A_1x04_P2.50mm_Vertical
Q7, Q8: Q_NMOS_GSD; SOT-23
R32, R34: 330; R_0603_1608Metric
R33: 10k; R_0603_1608Metric
TH1: Thermistor; R_0603_1608Metric
TP1, TP2, TP3: TestPoint; PinHeader_1x01_P1.00mm_Vertical
U4: STM32G431CBTx; LQFP-48_7x7mm_P0.5mm

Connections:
+3V3: C38.1, C39.1, FB1.2; also elsewhere on the board
/HallA: U4.43 (PB6); also elsewhere on the board
/HallB: U4.44 (PB7); also elsewhere on the board
/HallC: U4.45 (PB8-BOOT0); also elsewhere on the board
/MCU/3V3_MCU: C41.1, C42.1, C43.1, C44.1, D3.1 (A1), D3.2 (A2), FB1.1, FB2.2, J7.1, J8.1, J9.1, TH1.2, U4.1 (VBAT), U4.24 (VDD), U4.36 (VDD), U4.48 (VDD)
/MCU/3V3_MCU_A: C45.1, C46.1, FB2.1, U4.20 (VREF+), U4.21 (VDDA)
/MCU/DAC1: TP1.1, U4.12 (PA4)
/MCU/DAC2: TP2.1, U4.13 (PA5)
/MCU/DRV_CS: U4.46 (PB9); also elsewhere on the board
/MCU/DRV_EN: U4.2 (PC13); also elsewhere on the board
/MCU/DRV_MISO: U4.41 (PB4); also elsewhere on the board
/MCU/DRV_MOSI: U4.42 (PB5); also elsewhere on the board
/MCU/DRV_SCK: U4.40 (PB3); also elsewhere on the board
/MCU/FET_Temp: C40.1, R33.2, TH1.1, U4.6 (PF1)
/MCU/GLED_Gate: Q8.1 (G), U4.3 (PC14)
/MCU/RLED_Gate: Q7.1 (G), U4.4 (PC15)
/MCU/RX_BMS: J9.4, U4.25 (PB11)
/MCU/RX_HBD: J8.4, U4.11 (PA3)
/MCU/Rst: C47.1, J7.5, U4.7 (PG10-NRST)
/MCU/SWCLK: J7.2, U4.38 (PA14)
/MCU/SWDIO: J7.4, U4.37 (PA13)
/MCU/TX_BMS: J9.3, U4.22 (PB10)
/MCU/TX_HBD: J8.3, U4.10 (PA2)
/MCU/USB_D+: U4.34 (PA12); also elsewhere on the board
/MCU/USB_D-: U4.33 (PA11); also elsewhere on the board
/MCU/VA: U4.14 (PA6); also elsewhere on the board
/MCU/VB: U4.15 (PA7); also elsewhere on the board
/MCU/VC: U4.17 (PB1); also elsewhere on the board
/MotorTemp: U4.5 (PF0); also elsewhere on the board
/ThreePhaseBridge and Power/CUR_A: U4.16 (PB0); also elsewhere on the board
/ThreePhaseBridge and Power/CUR_B: U4.9 (PA1); also elsewhere on the board
/ThreePhaseBridge and Power/CUR_C: U4.8 (PA0); also elsewhere on the board
/ThreePhaseBridge and Power/FAULT: U4.39 (PA15); also elsewhere on the board
/ThreePhaseBridge and Power/INHA: U4.32 (PA10); also elsewhere on the board
/ThreePhaseBridge and Power/INHB: U4.31 (PA9); also elsewhere on the board
/ThreePhaseBridge and Power/INHC: U4.30 (PA8); also elsewhere on the board
/ThreePhaseBridge and Power/INLA: U4.29 (PB15); also elsewhere on the board
/ThreePhaseBridge and Power/INLB: U4.28 (PB14); also elsewhere on the board
/ThreePhaseBridge and Power/INLC: U4.27 (PB13); also elsewhere on the board
/Throttle: U4.18 (PB2); also elsewhere on the board
/VbusSense: U4.26 (PB12); also elsewhere on the board
GND: C38.2, C39.2, C40.2, C41.2, C42.2, C43.2, C44.2, C45.2, C46.2, C47.2, J7.3, J8.2, J9.2, Q7.2 (S), Q8.2 (S), R33.1, TP3.1, U4.19 (VSSA), U4.23 (VSS), U4.35 (VSS), U4.47 (VSS); also elsewhere on the board
unnamed: D3.3 (K1), R34.1
unnamed: D3.4 (K2), R32.1
unnamed: Q7.3 (D), R32.2
unnamed: Q8.3 (D), R34.2

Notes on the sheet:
ADC1_IN11
TIM1_CH3N
Req I/O: 2x UARTs (4 pins) 3x Timer capture inputs (Halls) 6x Timer PWM outputs (MC phases) 3x ADC inputs (phase current) 3x ADC inputs (phase voltage) 1x ADC input (bus voltage) 1x ADC input (throttle) 1x ADC input (fet temp) 1x ADC input (motor temp) 2x USB 3x SWD (SWCLK, SWDIO, Reset) ? 2x LEDs 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
DAC1_OUT2
TIM4_CH2
USART3_RX
SPI1_MOSI
ADC1_IN10
DAC1_OUT1
ADC2_IN3
ADC2_IN4
TIM1_CH2
SPI1_SCK
TIM1_CH2N
ADC2_IN12
ADC1_IN1/COMP3_INP
TIM4_CH3
100nF capacitance for each Vdd pin 4.7uF bulk for all Vdd pins
USART2_TX
ADC1_IN15/COMP4_INP
TIM4_CH1
TIM1_CH3
USART3_TX
ADC1_IN12
TIM1_CH1N
3x Timer capture 6x Timer pwm 3+3+1+1(+1)+1+1 = 10 (or 11)x ADC 2x USB 3x SWD (2x GPIO) (2x DAC) Total: 24 to 29 I/O
ADC2_IN2/COMP1_INP
TIM1_CH1
USART2_RX
SPI1_MISO
TIM1_BKIN
ADC2_IN10

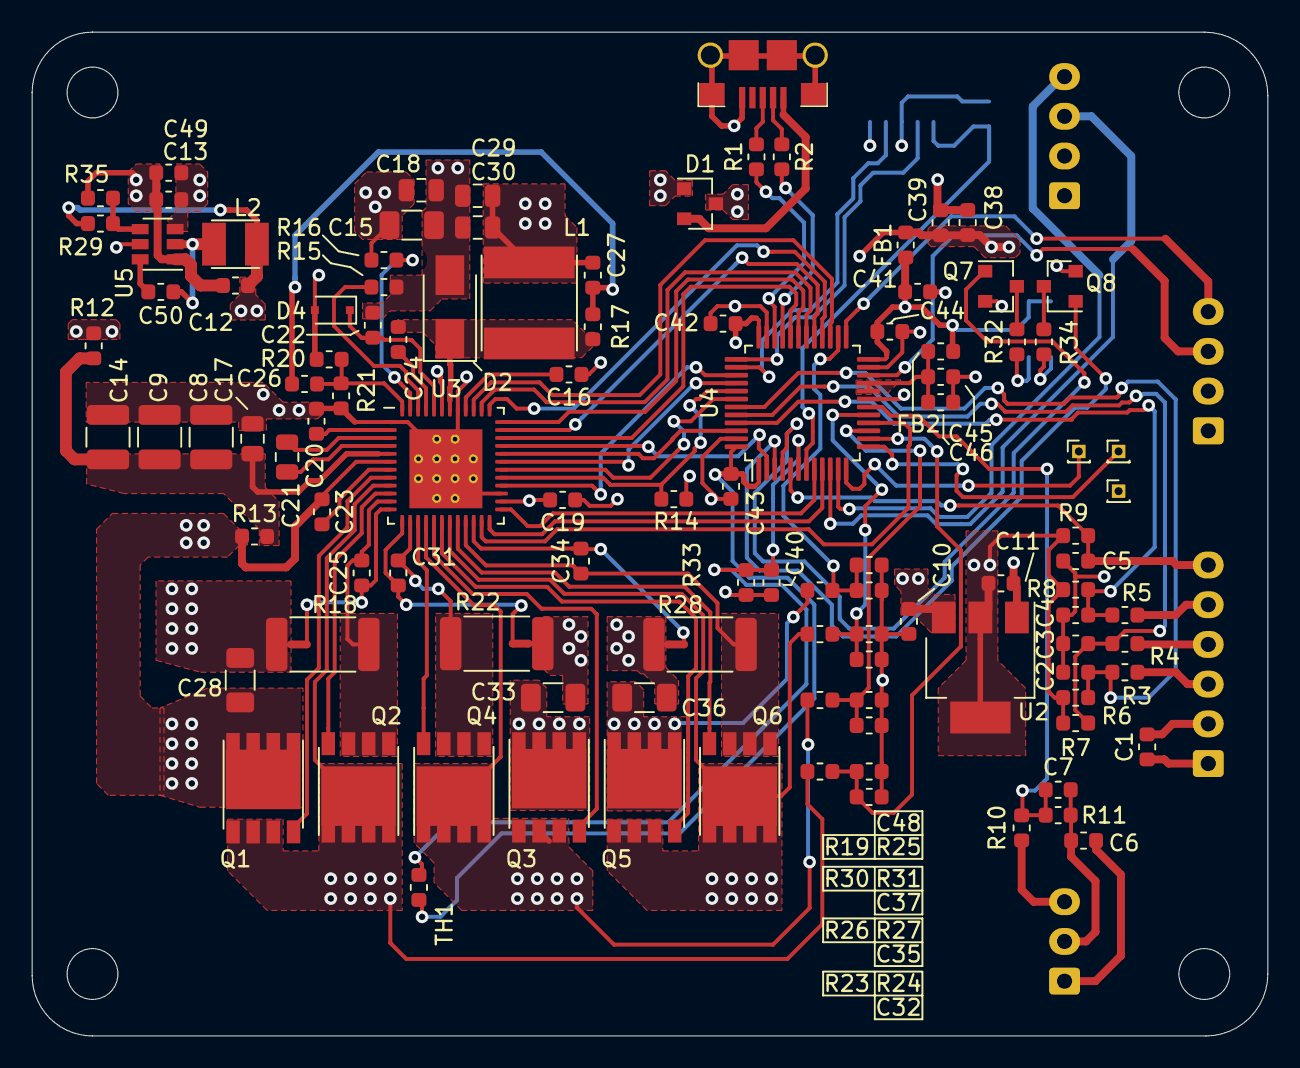
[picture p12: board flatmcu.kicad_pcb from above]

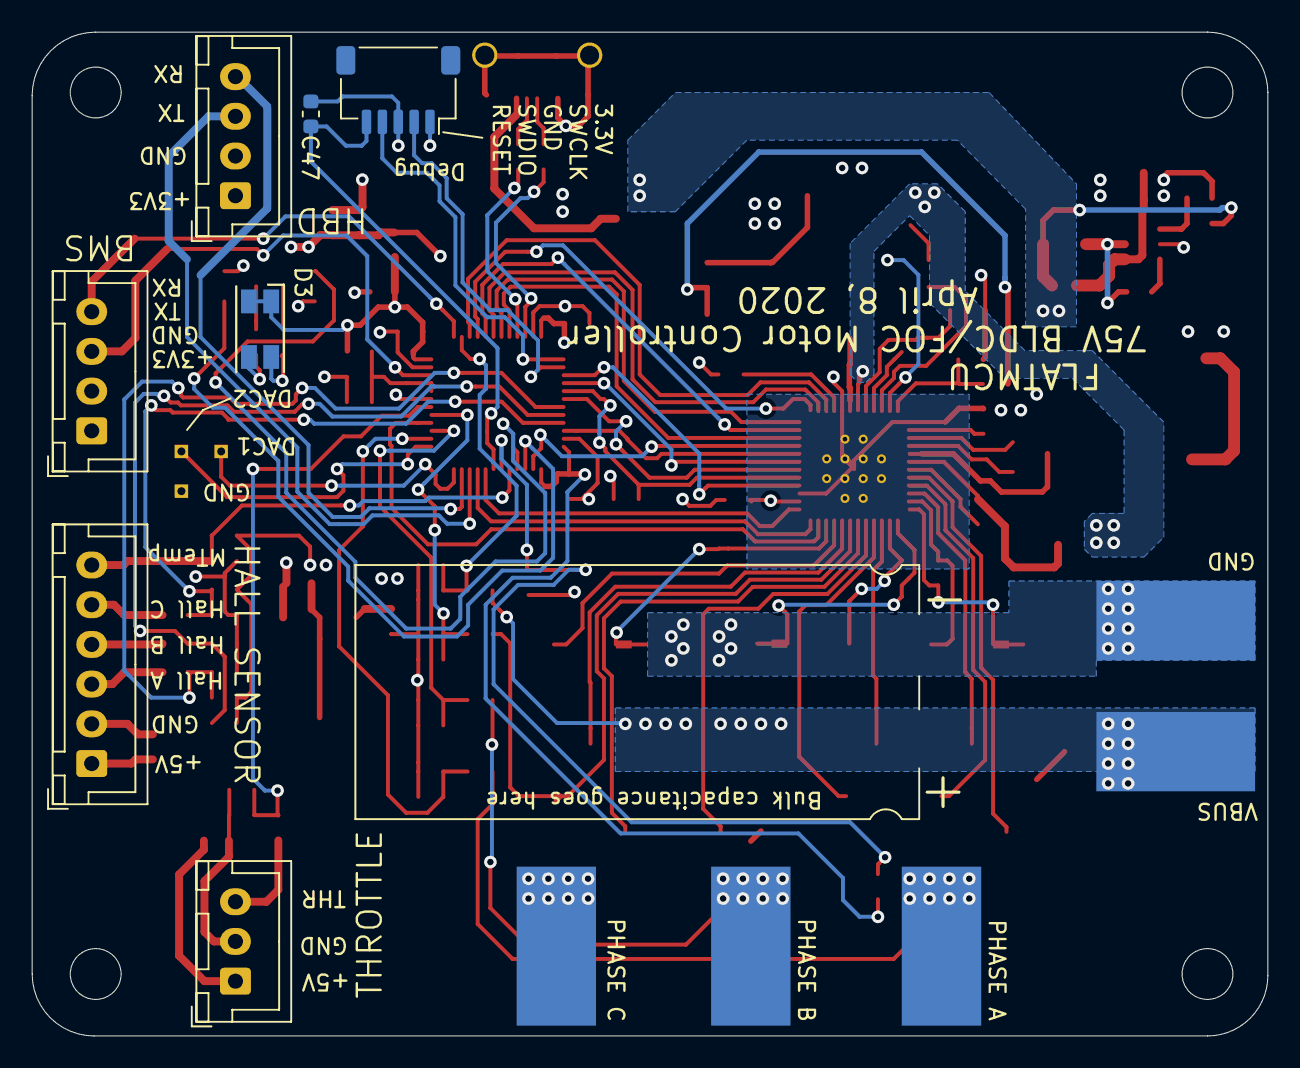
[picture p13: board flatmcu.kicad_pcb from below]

Board: 4 copper layers, 77.8 x 63.2 mm, 127 parts (12 on the bottom side), 88 nets.

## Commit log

2020-05-01 Initial import
    [MCU.sch, ThreePhaseBridge.sch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]
2022-09-16 Updated README.md - corrected link to kicad site
2023-11-07 updated for kicad 7
    [MCU.kicad_sch, ThreePhaseBridge.kicad_sch, flatmcu.kicad_pcb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]
2023-11-07 updated 3d model path
    [flatmcu.kicad_pcb]
